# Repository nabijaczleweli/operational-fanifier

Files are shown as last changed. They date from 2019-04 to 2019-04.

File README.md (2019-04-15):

# operational-fanifier 
This blows!

## What?

Automatic analogue tunable temperature-activated fan for the inside of one of my ATX supplies.

## Why?

The original fan is (a) loud and (b) runs continuously, this will probably help avoid the first through cutting down on the second.

## Whom with?

An [LM324N Op-Amp](//ti.com/lit/ds/symlink/lm324-n.pdf),
a [74HC32 Quad OR Gate](//mouser.com/ds/2/308/74HC32.REV1-102593.pdf),
a [LM335Z Kelvin-Calibrated Temperature Sensor](//ti.com/lit/ds/symlink/lm335.pdf),
and a handful of generics.

## How?

#### Schematic

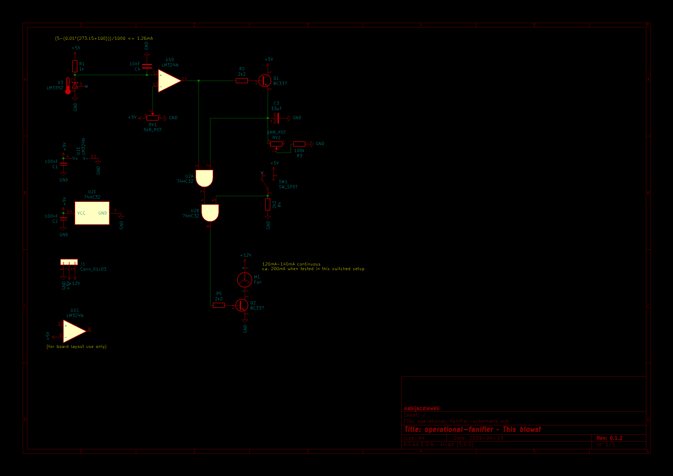
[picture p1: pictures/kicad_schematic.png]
Schematic picture export


#### Short description

Starting from the top-left, we can see the Temperature Sensor (`U3`), to be mounted onto the target heatsink, leading into an op-amp unit (`U1D`),
  which compares it to the customisable potentiometer (`RV1`) voltage divider.
As for the use of a quad op-amp when using only one unit thereof – these were vastly (15x/pc.) cheaper at my local shop,
  and have not been chosen due to any specific characteristics.

Thus, if the reading from the Sensor is higher than the pre-set voltage, the output will also go high, which will lead to two things:
  (a) pulling one input of the primary OR gate (`U2A`) high, and
  (b) charging the timing capacitor (`C3`) via the timing input transistor (`Q1`).

The timing capacitor's discharge rate can be controlled via the customisable potentiometer (`RV2`),
  which will, with the given `C1 = 33µF`, `R3 = 100kΩ`, and `RV2 = 1MΩ` values and the datasheet-specified threshold voltage of `Vₜₕ = 0.7V𝒸𝒸`
  as well as perfect linearity and full opening charge, vary between `(1 - 0.7) * 33µF * (100kΩ + 0) = 0.99s` and `(1 - 0.7) * 33µF * (100kΩ + 1MΩ) = 10.89s`.

The positive terminal of the timing capacitor is tied to the other input of the primary OR gate, meaning it will keep it active for longer than just the Sensor would.

The output fo the primary OR gate leads into one of the inputs of the secondary OR gate (`U2B`),
  whose second input is tied directly to a pulled-down bistable override switch (`SW1`),
  flipping whichof will turn on the fan (`M1`) regardless of any earlier autonomous stages (i.e. everything from the Sensor to the primary OR gate output).

Which means, that if either the override switch is on. the temperature sensor reads above the preuser-specified temperature,
  or the timer capacitor hasn't gone below the threshold voltage, the fan will be turned on via the primary transistor (`Q2`).

#### Layout

PCB layout picture export

The layout is very cramped due to my use of a very peculiar perfboard; it probably could've been solved much cleaner otherwise.

#### Model

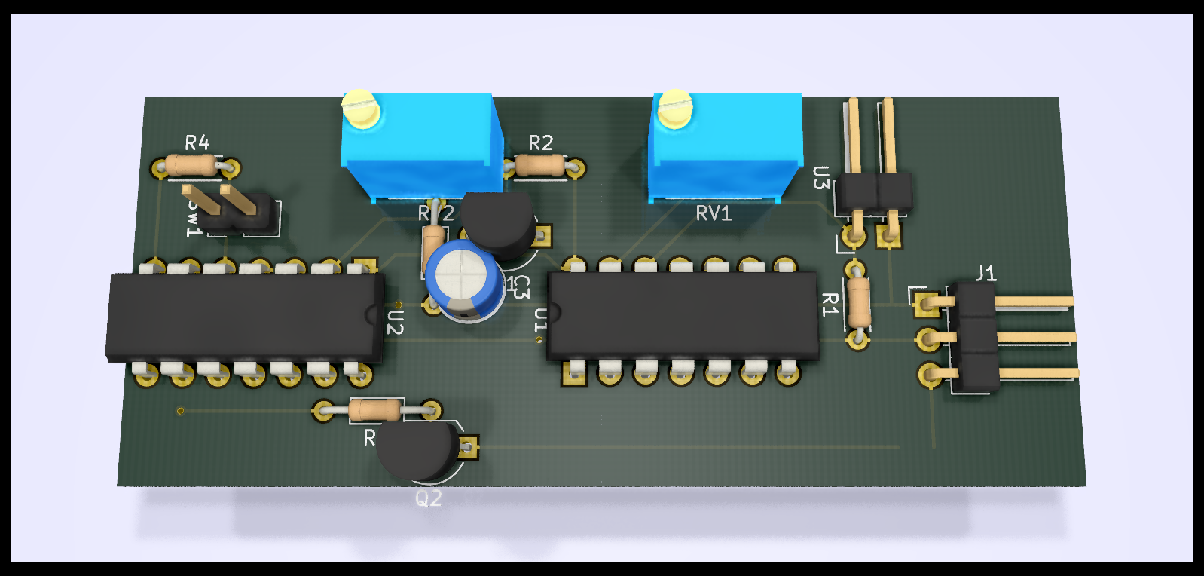
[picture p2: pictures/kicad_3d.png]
PCB layout 3D model


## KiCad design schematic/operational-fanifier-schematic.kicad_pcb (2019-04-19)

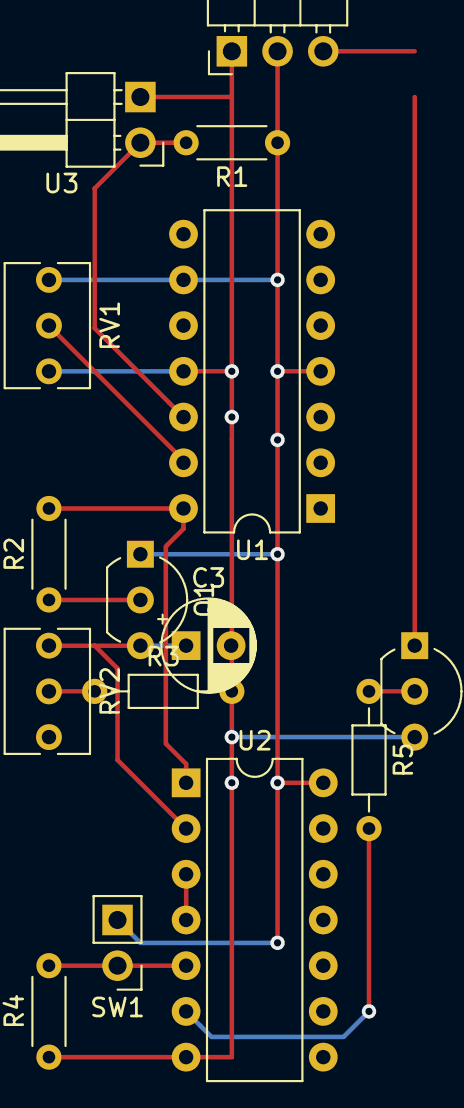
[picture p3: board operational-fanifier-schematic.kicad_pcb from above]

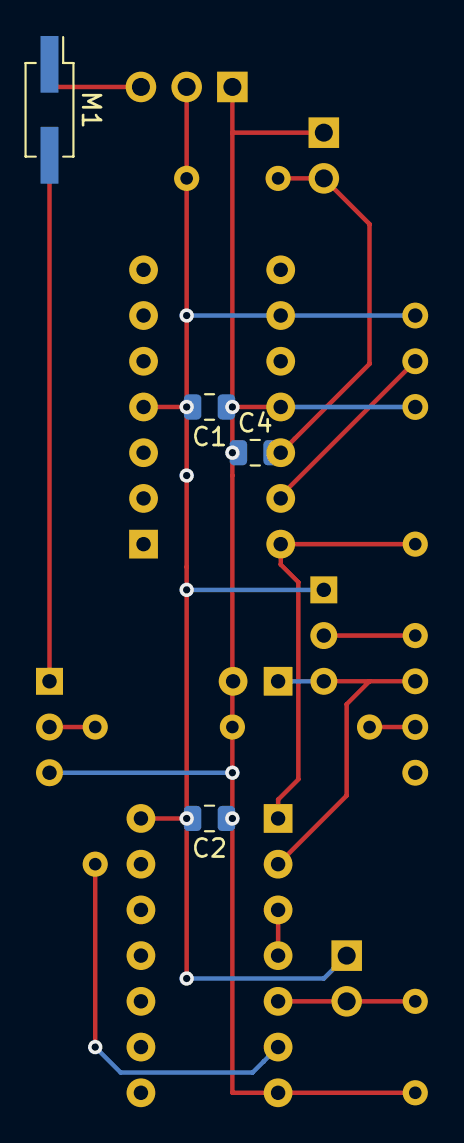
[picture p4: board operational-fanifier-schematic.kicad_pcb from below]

Board: 2 copper layers, 19 parts (4 on the bottom side), 14 nets.

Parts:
C1, C2: 100nF; C_0805_2012Metric
C3: 33µF; CP_Radial_D5.0mm_P2.50mm
C4: 10nF; C_0805_2012Metric
J1: Conn_01x03; PinHeader_1x03_P2.54mm_Horizontal
M1: Fan; PinHeader_2x01_P2.54mm_Vertical_SMD
Q1, Q2: BC337; TO-92_Inline_Wide
R1: 1k; R_Axial_DIN0204_L3.6mm_D1.6mm_P5.08mm_Horizontal
R2, R4: 2k2; R_Axial_DIN0204_L3.6mm_D1.6mm_P5.08mm_Horizontal
R3: 100k; R_Axial_DIN0204_L3.6mm_D1.6mm_P7.62mm_Horizontal
R5: 2k2; R_Axial_DIN0204_L3.6mm_D1.6mm_P7.62mm_Horizontal
RV1: 5kR_POT; Potentiometer_Bourns_3266Y_Vertical
RV2: 1MR_POT; Potentiometer_Bourns_3266Y_Vertical
SW1: SW_SPDT; PinHeader_1x02_P2.54mm_Vertical
U1: LM324N; DIP-14_W7.62mm
U2: 74HC32; DIP-14_W7.62mm
U3: LM335Z; PinHeader_1x02_P2.54mm_Horizontal

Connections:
+5V: C1.2, C2.2, J1.2, Q1.1, R1.1, RV1.3, U1.4, U1.9, U2.14
+12V: J1.3, M1.1
GND: C1.1, C2.1, C3.2, C4.1, J1.1, Q2.3, R3.2, R4.1, RV1.1, U1.11, U2.7, U3.1
unnamed: C3.1, Q1.3, RV2.3, U2.2
unnamed: C4.2, R1.2, U1.12, U3.2
unnamed: M1.2, Q2.1
unnamed: Q1.2, R2.1
unnamed: Q2.2, R5.1
unnamed: R2.2, U1.14, U2.1
unnamed: R3.1, RV2.2
unnamed: R4.2, SW1.2, U2.5
unnamed: R5.2, U2.6
unnamed: RV1.2, U1.13
unnamed: U2.3, U2.4

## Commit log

2019-02-24 Mostly-final layouted schematic
    [operational-fanifier-schematic.sch]
2019-02-24 Add layouted board
2019-02-24 Title b l o c c
    [operational-fanifier-schematic.sch]
2019-02-24 Add picture exports
    The render is absolutely *beautiul* though, like, holy shit
    [operational-fanifier-schematic.kicad_pcb]
2019-02-24 Include KiCad exports in README. Add plaintext explanation to README
2019-03-01 Move the transistor to below the fan. Add test results with transistored
    [operational-fanifier-schematic.kicad_pcb, operational-fanifier-schematic.sch]
2019-04-15 Use two-pin footprints where applicable. Use horizontal headers for M1 and U3
    [operational-fanifier-schematic.kicad_pcb, operational-fanifier-schematic.sch]
2019-04-15 Don't flip when not required
    [operational-fanifier-schematic.kicad_pcb]
2019-04-15 Bump version to 0.1.1 in exports
    [operational-fanifier-schematic.kicad_pcb, operational-fanifier-schematic.sch]
2019-04-19 I really should think these things through
    [operational-fanifier-schematic.kicad_pcb, operational-fanifier-schematic.sch]
2019-04-19 Bump version to 0.1.2
    [operational-fanifier-schematic.kicad_pcb, operational-fanifier-schematic.sch]

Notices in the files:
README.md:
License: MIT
